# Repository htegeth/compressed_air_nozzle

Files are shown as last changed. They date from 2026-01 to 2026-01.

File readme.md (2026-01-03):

#Ventilsteuerung

## Teileliste

| Produkt |Anzahl| Größe | Beschreibung | Kosten | Quelle |
|---|----|---|---|---|---|
|Gewindeschraube|2|M4 x 6mm| Zwei Gewindeschrauben um das Magnetventil an die Box festzuschrauben| 0,19€| [Bauhaus](https://www.bauhaus.info/gewindeschrauben/marinetech-gewindeschraube/p/23679276)
|Gewindeschraube|2|M2 x 4mm|Gewindeschrauben um das Relais an die Box zu schrauben
|Magnetventil| 
|Relais|

## Aufbau
Im Halloweenprojekt ist es vorgesehen, dass ein Drucklufteffekt eingebaut wird. Dazu wird an einem KOmpressor ein druckluftschlauch angeschlossen an dessen Ende ein Magnetventil befestigt ist. Im passenden Augenblick wird das Ventil geöffnet und ein Luftstoß erschrickt die ZUschauer.

Das Ventil ist ein günstiges 12V Magnetventil  von Amazon: [Heschen Magnetventil ](https://www.amazon.de/dp/B072ZZK9SD). Das Ventil ist vom Typ "normalerweise geschlossen" und öffnet sich wenn 12V Gleichspannung anliegt. Gesteuert werden soll das Ventil über einen Arduino bzw hier einen ATtiny85. Da dieser aber mit 12V betrieben wird, ist ein zusätzliches Gleichspannungsrelais erforderlich [Relais](https://www.amazon.de/dp/B07CNR7K9B). Das Relais wird im Normaly Open betriben, d.h. der Schalter ist normalerweise offen und es fließt kein Strom. So wird das Relais an das Magnentventil angeschlossen und der ATtiny am Relais und steuert dies.

Damit auch der Attiny mit strom versorgt wird bekommt er diesen über ein Stepdown Modul der 12V Stromversorgung für das Magnetrelais.

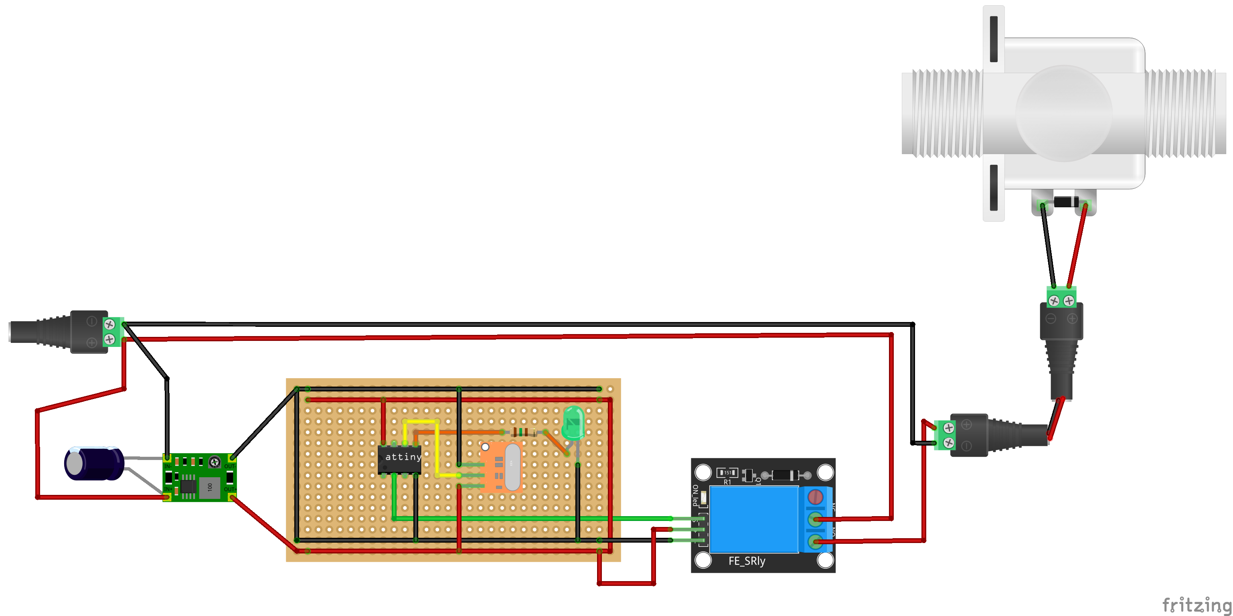
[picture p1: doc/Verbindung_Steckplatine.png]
Fritzing


In der Grafik ist der Schaltplan. Attiny wird mit dem Funkmodul verbunden und steuert das Relais. 
Der Code zum Auslösen des Relais ist die (3) ein 8 bit Wert der über RCSwitch dekodiert wurde.
ZUsätzlich wurde eine Kontroll-LED mit Widerstand angebracht und zwei Kondensatoren die in Reihe geschaltet, die Spannungsschwankungen durch das Öffnen und Schließen der Relais ausgleichen und Störungen herausfiltern, um den 433Mhz Sender und den Attiny zu schützen. E

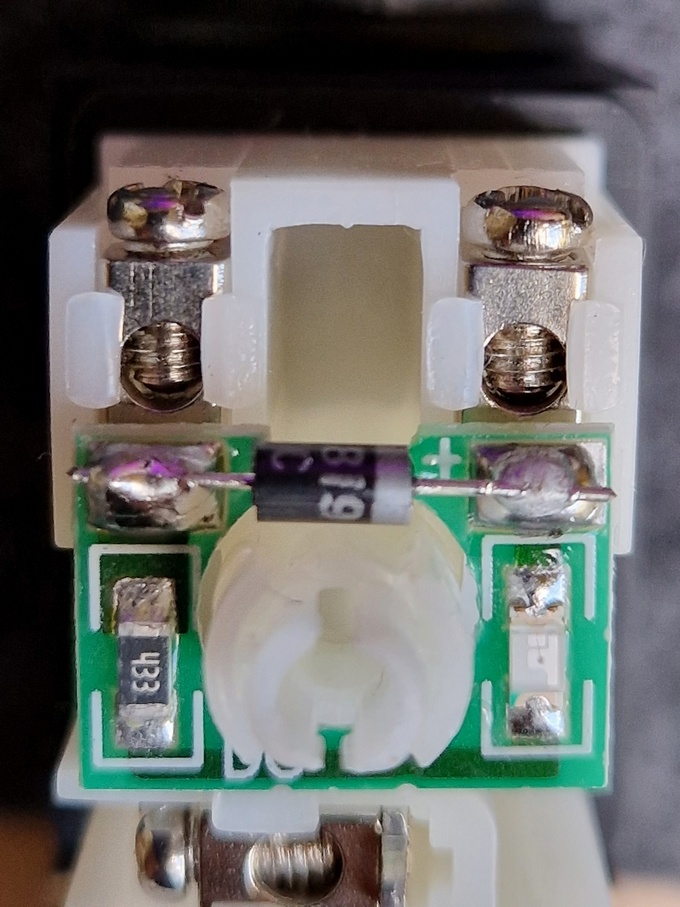
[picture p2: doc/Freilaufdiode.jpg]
Freilaufdiode


Eine Schottky Diode am Magnetventil verhindert, dass umgekehrte Spannung in die Schaltung eindringt. HIer muss die Kathode (Silberstreifen) an Plus und die Anode an Minus angeschlossen werden. Auf dem Bild zu sehen. wurde die Diode einfach auf die vorhandenen Lötpunkte gesetzt.

 Das verwendete Schalt-Relais hat eine Freilaufdiode integriert, bei billigen Relais sollte man darauf achten und hier ebenfalls eine Schottky Diode nachrüsten.

Verwendet werden ein 220Ohn widerstand. Ein 10µF Elko , ein 100 nF Kerko und eine 1N5819 Schottky Diode. Das Prinzip Freilaufdiode wird hier erklärt: [Mit der Freilaufdiode Rauschen reduzieren](https://resources.altium.com/de/p/using-flyback-diodes-relays-prevents-electrical-noise-your-circuits)

Wird das Signal erkannt, öffnet der Prozessor das Ventil für einen bestimmte Zeit, schließt es und wartet erneut auf das nächste Signal.

Da es für den Effekt wichtig sein kann regeln zu können, wie lange das Ventil auf ist, zb. 300 statt 100 Millisekunden gibt es einen zweiten Code. Dieser kann wie folgt aussehen:
99TTTT, eine sechstellige Zahl. Beginnend mit dem Startcode und den folgenden vier Ziffern welche die Dauer des Luftstoßes in Millisekunden darstellen. Dieser neue Wert wird im EEPROM abgelegt und steht bei Neustart wieder zur Verfügung.

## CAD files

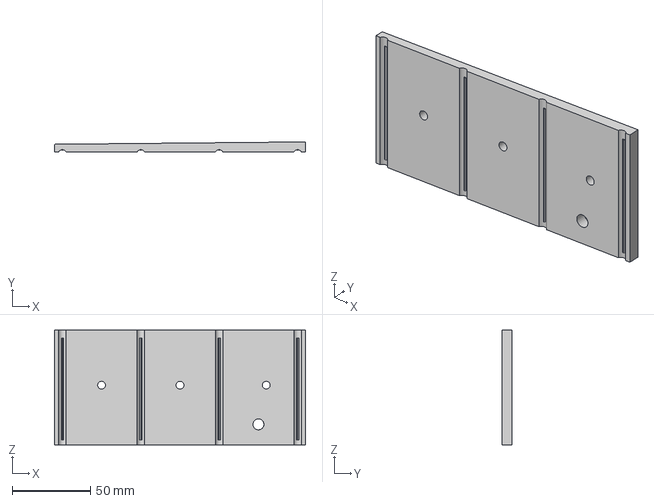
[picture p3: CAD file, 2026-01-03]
3dPrint/Zaun-Halter.3mf
160.0 x 6.50 x 73.0 mm

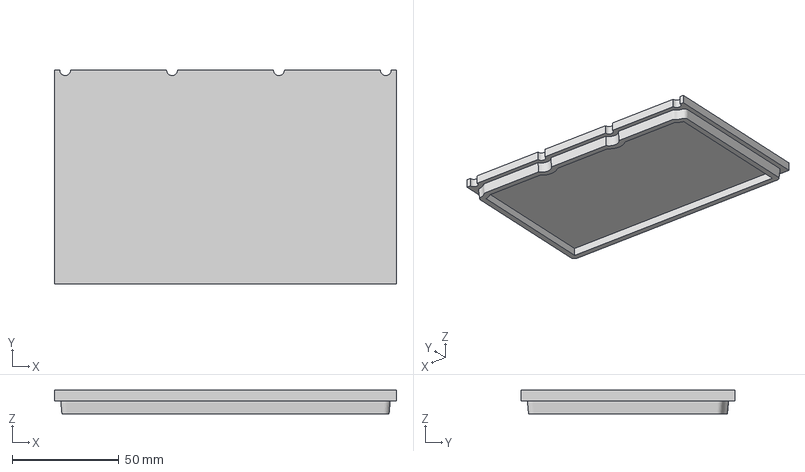
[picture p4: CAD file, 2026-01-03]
3dPrint/Deckel.3mf
160.0 x 100.0 x 11.0 mm

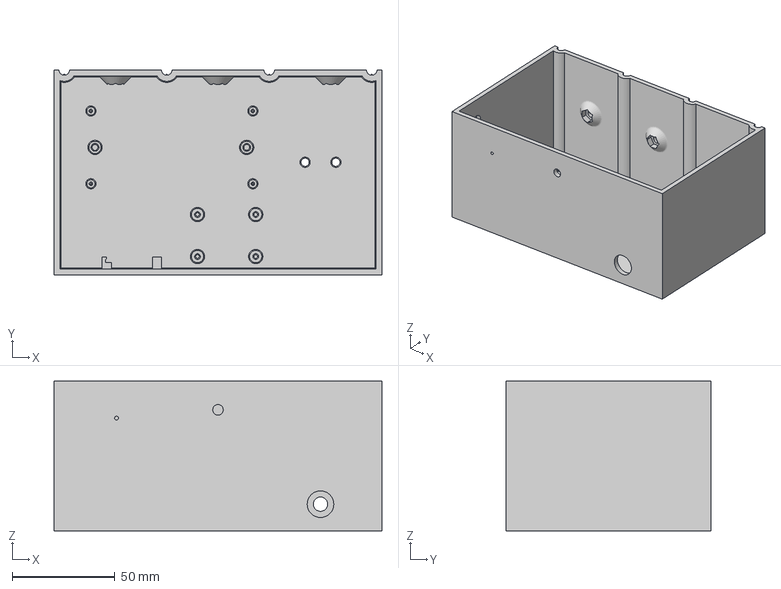
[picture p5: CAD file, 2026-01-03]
3dPrint/VentilBox_Gehäuse.3mf
160.0 x 100.0 x 73.0 mm

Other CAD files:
3dPrint/Körper8.3mf
3dPrint/Ventilbox v26.f3d

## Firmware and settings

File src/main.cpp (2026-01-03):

#include <Arduino.h>
#include <atRcRwitch.h>
#include <EEPROM.h>

// ATTiny 85 PINS
#define INTERRUPT_PIN   PCINT1     // Interrupt = PB1
#define VENTIL_PIN      PB3        // Relaisausgang
#define CONTROL_LED     PB0        // Status LED
#define PCINT_VECTOR    PCINT0_vect

// Befehlspräfixe
#define PREFIX_FLEX     77
#define PREFIX_CONFIG   99

// Konfiguration (über platformio.ini gesetzt)
const unsigned int druckluftDauerConf = DRUCKLUFTDAUER;
const unsigned long ventilCode = VENTIL_CODE;
const unsigned int druckluftDauerMin = DRUCKLUFTDAUER_MIN;
const unsigned int druckluftDauerMax = DRUCKLUFTDAUER_MAX;

RCSwitch mySwitch = RCSwitch();

static unsigned int druckluftDauer;
unsigned long currentCodeMain = 0;

void setup() {
  pinMode(CONTROL_LED, OUTPUT);
  pinMode(VENTIL_PIN, OUTPUT);

  cli();
  PCMSK |= (1 << INTERRUPT_PIN);
  GIMSK |= (1 << PCIE);
  pinMode(INTERRUPT_PIN, INPUT_PULLUP);
  mySwitch.enableReceive(0);
  sei();

  EEPROM.get(0, druckluftDauer);
  if (druckluftDauer == 0xFFFF || druckluftDauer < druckluftDauerMin || druckluftDauer > druckluftDauerMax) {
    druckluftDauer = druckluftDauerConf;
    EEPROM.put(0, druckluftDauerConf);
  }
}

ISR(PCINT_VECTOR) {
  // Muss so, da die Library Interrupt-Bearbeitung intern erfordert
  mySwitch.handleInterrupt();
}

void ventilOffen(unsigned int dauer) {
  if (dauer >= druckluftDauerMin && dauer <= druckluftDauerMax) {
    // HIGH aktiviert das Relais nur dann, wenn es sich um ein High-Level-Trigger-Relaismodul handelt;
    digitalWrite(CONTROL_LED, HIGH); 
    digitalWrite(VENTIL_PIN, HIGH); 
    delay(dauer);
    digitalWrite(VENTIL_PIN, LOW);
    digitalWrite(CONTROL_LED, LOW);
  }
}

void feedbackLed() {
  for (int i = 0; i < 5; i++) {
    digitalWrite(CONTROL_LED, HIGH);
    delay(50);
    digitalWrite(CONTROL_LED, LOW);
    delay(50);
  }
}

void loop() {
  if (mySwitch.available()) {
    currentCodeMain = mySwitch.getReceivedValue();
    mySwitch.resetAvailable();
  }

  unsigned long codePrefix = currentCodeMain / 10000;
  unsigned long codeSuffix = currentCodeMain % 10000;

  if (currentCodeMain == ventilCode) {
    ventilOffen(druckluftDauer);
  } 
  else if (codePrefix == PREFIX_FLEX) {
    ventilOffen(codeSuffix);
  } 
  else if (codePrefix == PREFIX_CONFIG) {
    feedbackLed();
    if (codeSuffix >= druckluftDauerMin && codeSuffix <= druckluftDauerMax) {
      if (codeSuffix != druckluftDauer) {
        druckluftDauer = codeSuffix;
        EEPROM.put(0, druckluftDauer);
      }
    }
  }

  currentCodeMain = 0; // Reset nach jedem Befehl
}

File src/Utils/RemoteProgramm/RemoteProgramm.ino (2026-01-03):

/*
 (!) Benutze den Sketch in der Arduino IDE oder schreibe eine eigene platformio.ini dafür.

 Wird verwendet um die Fernbedienung zu programmieren.
 Wichtig ist es die Fernbedienung ganz nah an den Sender zu halten. 
 Die Fernbedienung darf den Sender sogar berühren, sonst funktioniert die Übertragung nicht.
 Nicht jede Fernbedienung kann jedes Protokoll oder jede Bitlänge der Nachricht.

 Die Fernbedienung sollte vorher in den Programmiermodus gebracht werden. Bei den meisten Modellen mit vier Knöpfen geht das so:
 1. Knopf 1 (oder A) und 2 (B) gleichzeitig drücken bis die LED blinkt und ausgeht (das ist der Reset!) -> Knopf 1 nicht loslassen
 2. Knopf 1 weiter gedrückt halten  und Knopf 2  drei mal hintereinander drücken. Die LED sollte dann flackkern
 3. Unter mySwitch.send(n,24) den neuen Code eintragen und das Sketch auf den Arduino übertragen
 4. Knopf 1-4 (A-D) drücken und halten bis die LED nicht mehr blinkt sondern flackert.
*/

#include <RCSwitch.h>

RCSwitch mySwitch = RCSwitch();

void setup() {
  mySwitch.enableTransmit(3); //PIN 3
}

void loop() {
  mySwitch.setProtocol(1);
  mySwitch.send(770200, 24);
  delay(500);

}

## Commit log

2025-09-02 Aufgeräumt
    [Baugruppe-Horiz.cfg, Baugruppe_helmlichtbox.cfg, Bedienungshalter-Horiz-Druck.3mf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]
2025-09-11 Angepasst für den ersten Aufschlag
    [Verbindung.fzz]
